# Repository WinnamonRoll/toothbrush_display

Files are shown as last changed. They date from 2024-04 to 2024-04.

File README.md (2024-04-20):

# toothbrush showcase box

## background
I was contacted by a friend of my friend to help her design and build a simple interactive toothbrush showcase box for a dental care company. Although this project was supposed to be a simple small project, I was hesitant to accept the project as I am aware that I am an electronics noob. However, the hobbyist side of me told me to accept the project, as this project will be a great opportunity for me to revive my knowledge in mechatronics and embedded systems programming, which, admittedly, have become quite rusty since I graduated. Besides, I got paid for all the components.

As a person who has worked with similar projects before, my first instinct is to use an Arduino to control the showcase box. However, what is particularly challenging for me in this project is the circuitry. Previously, I used to make a circuit with my own hands, either by using jumper wires on a breadboard or putting each component on a prototype board and soldering them one-by-one. Needless to say that was very time consuming and also prone to errors. I remember that there were a couple of times in my university years that I had to pull an all-nighter to solder prototype circuit boards for class projects, and those were painful experiences. So, when I accepted this project, I told myself that I would not make a circuit board by hand anymore, but rather I would use EasyEDA to design my first PCB and also get it printed and shipped to me. Fortunately, the learning curve in designing a PCB is not as steep as I thought (at least for a simple circuit board like this) as there are plenty of useful learning resources on the internet. I was very excited when the parcel arrived at my house, and I think I did an okay job for my first PCB. Nevertheless, I still made some design flaws which I am working on the second version to correct them.

<p align="center">
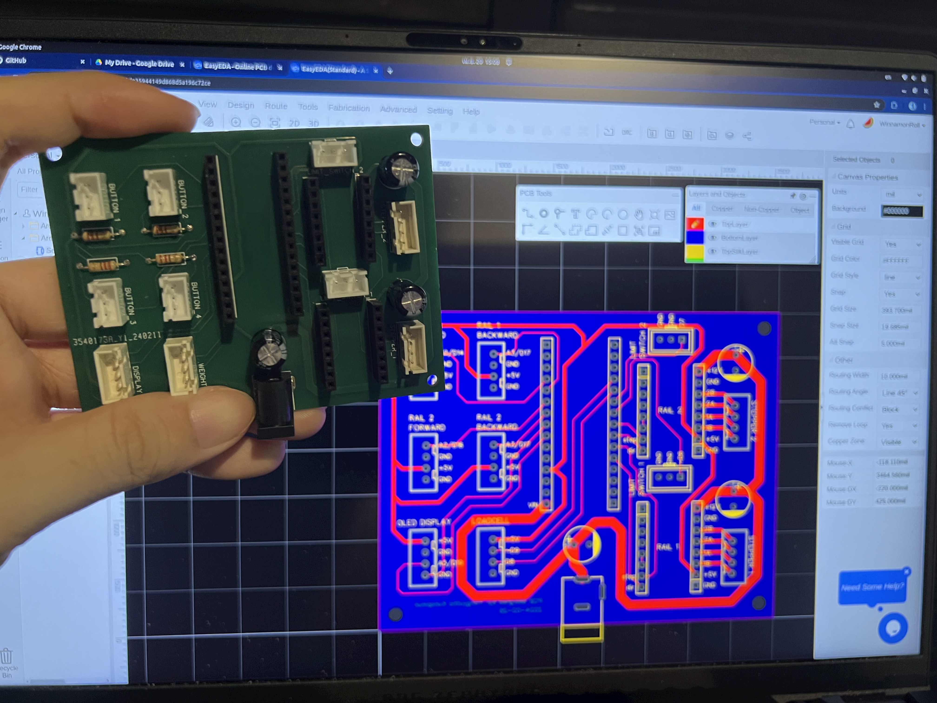
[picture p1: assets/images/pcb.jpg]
  
</p>

## project description
The toothbrushes will be moved back and forth using lead screw drives as customers interact with the box via buttons. Also, the customers can try using the toothbrush to brush the teeth model where the brushing weight will be monitored and shown on a mini OLED screen. This showcase box will allow customers to get a sense of how heavy they regularly brush their teeth so that they can choose their next toothbrush appropriately.

<p align="center">
  
</p>

## known design mistakes
- Originally, I designed the PCB to use with an Arduino Nano v3.0; however, I made a mistake: I assumed that the pin A4 and A5 of an Arduino Nano can also be used as digital pins. I circumvented this mistake by opting for an Arduino Nano Every, where both pin A4 and A5 can be used as a digital pin. Nevertheless, Arduino Nano Every is more expensive than an Arduino Nano clone, so in the second version I would like to correct this mistake.
- Some female JST XH2.54 headers on the PCB are not correctly placed. I have to flip the pins in the male headers to correct this mistake, but as a perfectionist I don't like this at all. It makes me upset.

## known issues
- The function void display_weight_in_grams(Adafruit_SSD1306, int, int), which is supposed to nicely format the brushing weight and display it on the Adafruit OLED screen, is bugged. The formatting works fine but sometimes there can be weird characters overlaid on the screen. Currently, I have no idea what causes this, so I think I will ask about it on the Arduino forum. If you know what causes this, please let me know.
- I noticed that sometimes when I move the box around in my room, the box will suddenly stop working: The Arduino, stepper motors, and buttons are still powered, but the OLED screen will be off and the lead screw will not move when I press a button. I suspect that this is due to the wiring of the OLED screen being loose, causing the screen to be disconnected and freeze the whole program loop. Turning the power off and on again will fix this issue.

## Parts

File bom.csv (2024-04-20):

ID | Name | Designator | Footprint | Quantity | Manufacturer Part | Manufacturer | Supplier | Supplier Part | Price
1 | WAFER-XH2.54-3PZZ | BUTTON_2,BUTTON_3,BUTTON_4,LIMIT_SWITCH_1,LIMIT_SWITCH_2,BUTTON_1 | CONN-TH_3P-P2.50_WAFER-XH2.54-3PZZ | 6 | WAFER-XH2.54-3PZZ | XUNPU(讯普) | LCSC | C5374805 | 0.016
2 | 100uF | C1,C2,C3 | CAP-TH_BD8.0-P3.50-D0.6-FD | 3 | KM1H101MF115A00CV0 | HUAWEI(华威集团) | LCSC | C190655 | 0.046
3 | XH-4A_C2904944 | DISPLAY,WEIGHT,STEPPER_1,STEPPER_2 | CONN-TH_4P-P2.50-XH2.54-4P | 4 | XH-4A | DEALON(德艺隆) | LCSC | C2904944 | 0.016
4 | KH-2.54FH-1X8P-H8.5 | U4,U5,U7,U8 | HDR-TH_8P-P2.54-V-F | 4 | KH-2.54FH-1X8P-H8.5 | kinghelm(金航标) | LCSC | C2905417 | 0.081
5 | KH-2.54FH-1X15P-H8.5 | U1,U2 | HDR-TH_15P-P2.54-V-F | 2 | KH-2.54FH-1X15P-H8.5 | kinghelm(金航标) | LCSC | C2932676 | 0.12
6 | 220Ω | R1,R2,R3,R4 | RES-TH_BD2.7-L6.2-P10.20-D0.4 | 4 | CR1/4W-220Ω±5%-ST26 | VO(翔胜) | LCSC | C2894616 | 0.003

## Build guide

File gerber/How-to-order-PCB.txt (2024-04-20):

How to Order PCB

Please refer to:
https://docs.easyeda.com/en/PCB/Order-PCB

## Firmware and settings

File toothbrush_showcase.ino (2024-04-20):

/*
 author: Yongyutha Kunapinun
version: 1.0.1
   note: for PCB version 1.0 with Arduino Nano Every
*/
#include <SPI.h>
#include <Wire.h>
#include <Adafruit_GFX.h>
#include <Adafruit_SSD1306.h>
#include <HX711.h>

#define RAIL_1_STP_PIN 3
#define RAIL_2_STP_PIN 5
#define RAIL_1_DIR_PIN 2
#define RAIL_2_DIR_PIN 4
// These two variables keep track of where the moving blocks are on rail 1 and rail 2, respectively
int rail_1_abs_stp = -1;
int rail_2_abs_stp = -1;
// delay parameters below are used for toggle-to-move mode
// maximum value of the step delay ramp (when a stepper is at its slowest)
#define MAX_STEP_DELAY 1000
// minimum value of the step delay ramp (when a stepper is at its fastest)
#define MIN_STEP_DELAY 250
// slope of the step delay ramp (must be negative)
#define STEP_RAMP_DOWN_SLOPE -10
#define MAX_RAIL_1_ABS_STP 15000
#define MAX_RAIL_2_ABS_STP 5000
#define MAX_RAIL_STP 15000
#define RAIL_1_LIM_SW_PIN 6
#define RAIL_2_LIM_SW_PIN 7
#define RAIL_1_FWD_BTN_PIN 14
#define RAIL_1_BWD_BTN_PIN 15
#define RAIL_2_FWD_BTN_PIN 16
#define RAIL_2_BWD_BTN_PIN 17
// OLED display width, in pixels
#define SCREEN_WIDTH 128
// OLED display height, in pixels
#define SCREEN_HEIGHT 32
// Declaration for an SSD1306 display connected to I2C (SDA, SCL pins)
// The pins for I2C are defined by the Wire-library. 
// On an arduino UNO:       A4(SDA), A5(SCL)
// On an arduino MEGA 2560: 20(SDA), 21(SCL)
// On an arduino LEONARDO:   2(SDA),  3(SCL), ...
// Reset pin # (or -1 if sharing Arduino reset pin)
#define OLED_RESET -1
//< See datasheet for Address; 0x3D for 128x64, 0x3C for 128x32
#define SCREEN_ADDRESS 0x3C
Adafruit_SSD1306 display(SCREEN_WIDTH, SCREEN_HEIGHT, &Wire, OLED_RESET);
#define DISPLAY_WEIGHT_DIGITS 6
#define LOADCELL_DOUT_PIN 21
#define LOADCELL_SCK_PIN 20
// depends on each loadcell, obained from calibration 
#define WEIGHT_SCLAE_FACTOR 100.82
HX711 scale;

int ramp_down_step_delay(int min_delay, int max_delay, int down_slope, int step) {
  if (min_delay < 0) {
    Serial.println("min_delay must not be negative");
    return -1;
  }
  if (max_delay < 0) {
    Serial.println("max_delay must not be negative");
    return -1;
  }
  if (max_delay < min_delay) {
    Serial.println("max_delay must not be less than min_delay");
    return -1;
  }
  if (down_slope > 0) {
    Serial.println("down_slope must be negative");
    return -1;
  }
  if (step < 0) {
    Serial.println("step must not be negative");
    return -1;
  }
  if (step < (min_delay-max_delay)/down_slope) {
    return max_delay+down_slope*step;
  } else if (min_delay > 100){
    return min_delay;
  } else {
    Serial.println("step delay must not be less than 100 microseconds");
    return -1;
  }
}

void step_backward(int stepper_number, int step_delay) {
  if (step_delay < 100) {
    Serial.println("step_delay must not be less than 100 microseconds");
    return -1;
  }
  if (stepper_number == 1) {
    digitalWrite(RAIL_1_DIR_PIN, HIGH);
    digitalWrite(RAIL_1_STP_PIN, HIGH);
    delayMicroseconds(step_delay);
    digitalWrite(RAIL_1_STP_PIN, LOW);
    delayMicroseconds(step_delay);
    return 0; 
  } else if (stepper_number == 2) {
    digitalWrite(RAIL_2_DIR_PIN, HIGH);
    digitalWrite(RAIL_2_STP_PIN, HIGH);
    delayMicroseconds(step_delay);
    digitalWrite(RAIL_2_STP_PIN, LOW);
    delayMicroseconds(step_delay);
    return 0; 
  } else {
    Serial.println("invalid stepper motor number");
    return -1;
  }
}

int step_forward(int stepper_number, int step_delay) {
  if (step_delay < 100) {
    Serial.println("step_delay must not be less than 100 microseconds");
    return -1;
  }
  if (stepper_number == 1) {
    digitalWrite(RAIL_1_DIR_PIN, LOW);
    digitalWrite(RAIL_1_STP_PIN, HIGH);
    delayMicroseconds(step_delay);
    digitalWrite(RAIL_1_STP_PIN, LOW);
    delayMicroseconds(step_delay);
    return 0; 
  } else if (stepper_number == 2) {
    digitalWrite(RAIL_2_DIR_PIN, LOW);
    digitalWrite(RAIL_2_STP_PIN, HIGH);
    delayMicroseconds(step_delay);
    digitalWrite(RAIL_2_STP_PIN, LOW);
    delayMicroseconds(step_delay);
    return 0;
  } else {
    Serial.println("invalid stepper motor number");
    return -1;
  }
}

void display_text(Adafruit_SSD1306 display, char *string){
  // Clear the buffer
  display.clearDisplay();
  display.setTextSize(1);
  display.setTextColor(SSD1306_WHITE);
  display.setCursor(10, 0);
  display.println(string);
  display.display();
}

void display_weight_in_grams(Adafruit_SSD1306 display, int weight) {
  display.clearDisplay();
  display.setTextSize(2); // Draw 2X-scale text
  display.setTextColor(SSD1306_WHITE);
  display.setCursor(10, 0);
  if (weight <= 0) {
    display.print(0);
    display.println(" g");
  } else {
    display.print(weight);
    display.println(" g");
  }
  display.display();
}

void display_weight_in_grams(Adafruit_SSD1306 display, int digits, int weight) {
  // this function still has some bugs
  //Serial.print("weight: ");
  //Serial.println(weight);
  display.clearDisplay();
  display.setTextSize(2);
  display.setTextColor(SSD1306_WHITE);
  display.setCursor(10, 0);
  if (digits <= 0) {
    Serial.println(F("error: number of digits must be at least 1"));
    return;
  }
  const int str_len = digits + (digits-1)/3 + 1;
  char *display_weight = (char*) malloc(sizeof(char) * str_len);
  for (int i = 0; i < str_len; i++) {
    if (i < str_len - 1) {
      *(display_weight + sizeof(char) * i) = ' ';
    } else {
      *(display_weight + sizeof(char) * i) = '\0';
    }
  }
  if (weight <= 0) {
    *(display_weight + (str_len - 2)) = '0';
  } else {
    for(int i = str_len - 2; weight > 0 && i >= 0; i--) {
      if ((str_len - 1 - i) % 4 == 0) {
        *(display_weight + i) = ',';
      }
      else {
        *(display_weight + i) = '0' + weight % 10;
        weight /= 10;
      }
    }
  }
  display.print(display_weight);
  display.println(" g");
  // Serial.print(display_weight);
  // Serial.println(" g");
  display.display();
  free(display_weight);
}

void setup() {
  // put your setup code here, to run once:
  Serial.begin(57600);
  pinMode(RAIL_1_STP_PIN, OUTPUT);
  pinMode(RAIL_2_STP_PIN, OUTPUT);
  pinMode(RAIL_1_DIR_PIN, OUTPUT);
  pinMode(RAIL_2_DIR_PIN, OUTPUT);
  pinMode(RAIL_1_LIM_SW_PIN, INPUT_PULLUP);
  pinMode(RAIL_2_LIM_SW_PIN, INPUT_PULLUP);
  pinMode(RAIL_1_FWD_BTN_PIN, INPUT_PULLUP);
  pinMode(RAIL_1_BWD_BTN_PIN, INPUT_PULLUP);
  pinMode(RAIL_2_FWD_BTN_PIN, INPUT_PULLUP);
  pinMode(RAIL_2_BWD_BTN_PIN, INPUT_PULLUP);
  pinMode(LED_BUILTIN, OUTPUT);
  if(!display.begin(SSD1306_SWITCHCAPVCC, SCREEN_ADDRESS)) {
    Serial.println(F("SSD1306 allocation failed"));
    exit(0);
  }
  // Show initial display buffer contents on the screen --
  // the library initializes this with an Adafruit splash screen.
  display.display();
  delay(2000); // Pause for 2 seconds
  display_text(display, "setting up...");
  for(int i = 0; i < MAX_RAIL_STP; i++) {
    //int tik = micros();
    if (digitalRead(RAIL_1_LIM_SW_PIN) == LOW) {
      break;
    }
    step_backward(1, ramp_down_step_delay(MIN_STEP_DELAY, MAX_STEP_DELAY, STEP_RAMP_DOWN_SLOPE, i));
    // int tok = micros();
    // Serial.print("time per step in homing rail 1: ");
    // Serial.println(tok-tik);
  }
  rail_1_abs_stp = 0;
  for(int i = 0; i < MAX_RAIL_STP; i++) {
    //int tik = micros();
    if (digitalRead(RAIL_2_LIM_SW_PIN) == LOW) {
      break;
    }
    step_backward(2, ramp_down_step_delay(MIN_STEP_DELAY, MAX_STEP_DELAY, STEP_RAMP_DOWN_SLOPE, i));
    // int tok = micros();
    // Serial.print("time per step in homing rail 2: ");
    // Serial.println(tok-tik);
  }
  rail_2_abs_stp = 0;
  display.clearDisplay();
  display_text(display, "calibrating...");
  scale.begin(LOADCELL_DOUT_PIN, LOADCELL_SCK_PIN);
  scale.tare();
  scale.set_scale(100.82);
  delay(3000);
  display.clearDisplay();
}

int rail_1_fwd_btn;
int rail_1_bwd_btn;
int rail_2_fwd_btn;
int rail_2_bwd_btn;
enum move_states {
  NONE,
  RAIL_1_FWD,
  RAIL_1_BWD,
  RAIL_2_FWD,
  RAIL_2_BWD
};
enum move_states move_state = NONE;
// consecutive relative step count variable
int consec_rel_stp = 0;

void loop() {
  // put your main code here, to run repeatedly:
  //int tik = micros();
  rail_1_fwd_btn = digitalRead(RAIL_1_FWD_BTN_PIN);
  rail_1_bwd_btn = digitalRead(RAIL_1_BWD_BTN_PIN);
  rail_2_fwd_btn = digitalRead(RAIL_2_FWD_BTN_PIN);
  rail_2_bwd_btn = digitalRead(RAIL_2_BWD_BTN_PIN);
  if (rail_1_fwd_btn == LOW || rail_1_bwd_btn == LOW || rail_2_fwd_btn == LOW || rail_2_bwd_btn == LOW) {
    digitalWrite(LED_BUILTIN, HIGH);
  } else {
    digitalWrite(LED_BUILTIN, LOW);
  }

  if (rail_1_fwd_btn == LOW && rail_1_abs_stp < MAX_RAIL_1_ABS_STP) {
    if (move_state == NONE) {
        display_text(display, "moving...");
    }
    if (move_state != RAIL_1_FWD){
      move_state = RAIL_1_FWD;
      consec_rel_stp = 0;
    }
    step_forward(1, ramp_down_step_delay(MIN_STEP_DELAY, MAX_STEP_DELAY, STEP_RAMP_DOWN_SLOPE, consec_rel_stp++));
    rail_1_abs_stp += 1;
  } else if (rail_1_bwd_btn == LOW && rail_1_abs_stp > 0) {
    if (move_state == NONE) {
        display_text(display, "moving...");
    }
    if (move_state != RAIL_1_BWD){
      move_state = RAIL_1_BWD;
      consec_rel_stp = 0;
    }
    step_backward(1, ramp_down_step_delay(MIN_STEP_DELAY, MAX_STEP_DELAY, STEP_RAMP_DOWN_SLOPE, consec_rel_stp++));
    rail_1_abs_stp -= 1;
  } else if (rail_2_fwd_btn == LOW && rail_2_abs_stp < MAX_RAIL_2_ABS_STP) {
    if (move_state == NONE) {
        display_text(display, "moving...");
    }
    if (move_state != RAIL_2_FWD){
      move_state = RAIL_2_FWD;
      consec_rel_stp = 0;
    }
    step_forward(2, ramp_down_step_delay(MIN_STEP_DELAY, MAX_STEP_DELAY, STEP_RAMP_DOWN_SLOPE, consec_rel_stp++));
    rail_2_abs_stp += 1;
  } else if (rail_2_bwd_btn == LOW && rail_2_abs_stp > 0) {
    if (move_state == NONE) {
        display_text(display, "moving...");
    }
    if (move_state != RAIL_2_BWD){
      move_state = RAIL_2_BWD;
      consec_rel_stp = 0;
    }
    step_backward(2, ramp_down_step_delay(MIN_STEP_DELAY, MAX_STEP_DELAY, STEP_RAMP_DOWN_SLOPE, consec_rel_stp++));
    rail_2_abs_stp -= 1;
  } else {
    move_state = NONE;
    consec_rel_stp = 0;
    display_weight_in_grams(display, scale.get_units());
    //display_weight_in_grams(display, DISPLAY_WEIGHT_DIGITS, scale.get_units());
  }
  // int tok = micros();
  // Serial.print("time per step in main loop: ");
  // Serial.println(tok-tik);
}

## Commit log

2024-04-20 Add pcb.jpg to /assets/images
2024-04-20 added gerber, pick and place, and bom files
    [Drill_PTH_Through.DRL, Drill_PTH_Through_Via.DRL, Gerber_BoardOutlineLayer.GKO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]
